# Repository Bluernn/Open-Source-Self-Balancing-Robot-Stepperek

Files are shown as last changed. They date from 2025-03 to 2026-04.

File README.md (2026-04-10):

# Open Source Self-Balancing Robot "Stepperek"

<p align="center">
  Self-balancing robot
</p>

This repository contains an open-source project for a self-balancing robot designed for educational purposes and learning control systems. The project includes both hardware and software components.
## Repository Contents

- **3D Models**  
It contains 3D models of the robot's wheels and motor mounts for 3D printing or further modifications.

- **Schematic and PCB**  
Includes the electrical schematic and all necessary files for manufacturing the PCB.

- **BalancingRobot**  
Contains the complete control program for the self-balancing robot, developed using ESP-IDF v5.2.1. This folder includes the source code and all required files to compile the project.

https://www.youtube.com/watch?v=AlN4MXNQWd8

Shield: [][cc-by-nc]

This work is licensed under a
[Creative Commons Attribution-NonCommercial 4.0 International License][cc-by-nc].

[][cc-by-nc]

[cc-by-nc]: https://creativecommons.org/licenses/by-nc/4.0/
[cc-by-nc-image]: https://licensebuttons.net/l/by-nc/4.0/88x31.png
[cc-by-nc-shield]: https://img.shields.io/badge/License-CC%20BY--NC%204.0-lightgrey.svg

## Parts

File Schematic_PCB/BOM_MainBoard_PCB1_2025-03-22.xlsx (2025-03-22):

No. | Quantity | Comment | Designator | Footprint | Value | Manufacturer Part | Manufacturer | Supplier Part | Supplier
1 | 2 | MY-18650-01 | BT1,BT2 | BAT-TH_MY-18650-01 |  | MY-18650-01 | MYOUNG(美阳) | C2979183 | LCSC
2 | 3 | 10uF | C2,C9,C10 | CASE-A_3216 | 10uF | CA45A-A-16V-10uF-K | CEC(振华新云) | C129279 | LCSC
3 | 7 | 100nF | C8,C20,C21,C35,C37,C39,C40 | C0805 | 100nF | 0805B104K500NT | FH-BK(风华邦科) | C2830721 | LCSC
4 | 1 | 22uF | C12 | CASE-A_3216 | 22uF | CA45-A-10V-22uF-K | CEC(振华新云) | C129272 | LCSC
5 | 6 | 220uF | C19,C26,C32,C34,C38,C41 | CAP-TH_BD6.3-P2.50-D1.0-FD | 220uF | ERS1EM221E11OT | AISHI(艾华集团) | C141282 | LCSC
6 | 2 | 22nF | C22,C28 | C0805 | 22nF | CL21B223KBANNNC | SAMSUNG(三星) | C1729 | LCSC
7 | 8 | 100nF | C23,C24,C25,C27,C29,C30,C31,C33 | C0805 | 100nF | CC0805KRX7R9BB104 | YAGEO(国巨) | C49678 | LCSC
8 | 1 | 680uF | C36 | CAP-TH_BD10.0-P5.00-D1.0-FD | 680uF | ERF1EM681G16OT | AISHI(艾华集团) | C106522 | LCSC
9 | 1 | SS54 | D2 | SMA_L4.4-W2.8-LS5.4-R-RD |  | SS54 | MDD | C22452 | LCSC
10 | 1 | 1N5821RLG | D3 | DO-201AD_BD5.3-L8.4-P12.50-D1.4-RD |  | 1N5821RLG | onsemi(安森美) | C9119 | LCSC
11 | 1 | MSS1P3-M3/89A | D17 | MICROSMP_L2.2-W1.3-LS2.5-RD |  | MSS1P3-M3/89A | VISHAY(威世) | C111315 | LCSC
12 | 1 | 2.54-1*3P针 | H1 | HDR-TH_3P-P2.54-V-M-1 |  | 2.54-1*3P针 | BOOMELE(博穆精密) | C49257 | LCSC
13 | 1 | PM2.54-1*4 | H2 | HDR-TH_4P-P2.54-V-F |  | PM2.54-1*4 | ZHOURI(洲日) | C5116530 | LCSC
14 | 1 | DC3-10P | JTAG | CONN-TH_10P-P1.27_DC3-10P |  | DC3-10P |  | C9900016558 | LCSC
15 | 1 | 2.2uH | L5 | IND-SMD_L2.5-W2.0 | 2.2uH | 252012CDMCDDS-2R2MC | Sumida(胜美达) | C351245 | LCSC
16 | 1 | 100uH | L6 | IND-SMD_L12.3-W12.3_SMDRI127 | 100uH | SMDRI127-101MT | SXN(顺翔诺) | C10150 | LCSC
17 | 2 | 17-21VRD/TR8 | LED1,LED3 | LED0805-R-RD |  | 17-21VRD/TR8 | EVERLIGHT(亿光) | C264415 | LCSC
18 | 2 | SZYY0805YG | LED2,LED6 | LED0805-R-RD_GREEN |  | SZYY0805YG | yongyu(永裕光电) | C434435 | LCSC
19 | 1 | HDR-F-2.54_2x3 | PROGRAMMER | HDR-TH_6P-P2.54-V-F-R2-C3-S2.54
20 | 5 | 1kΩ | R7,R11,R12,R20,R37 | R0805 | 1kΩ | RMC08051K5%N | Tyohm(幸亚电阻) | C269727 | LCSC
21 | 1 | 400mΩ | R10 | R0805 | 400mΩ | CR0805JR400P05Z | EVER OHMS(天二科技) | C175750 | LCSC
22 | 1 | 1.5kΩ | R13 | R0805 | 1.5kΩ | RMC08051.5K5%N | Tyohm(幸亚电阻) | C325846 | LCSC
23 | 2 | 5.1kΩ | R15,R16 | R0805 | 5.1kΩ | CR0805-FX-5101ELF | BOURNS | C204548 | LCSC
24 | 3 | 10kΩ | R21,R29,R36 | R0805 | 10kΩ | ARG05FTC1002 | Viking(光颉) | C217770 | LCSC
25 | 1 | 100Ω | R22 | R0805 | 100Ω | AECR0805F100RK9 | RESI(开步睿思） | C328380 | LCSC
26 | 3 | 2.2kΩ | R27,R30,R31 | R0805 | 2.2kΩ | 0805W8F2201T5E | UNI-ROYAL(厚声) | C17520 | LCSC
27 | 1 | 33kΩ | R28 | R0805 | 33kΩ | 0805W8F3302T5E | UNI-ROYAL(厚声) | C17633 | LCSC
28 | 4 | 1Ω | R32,R33,R34,R35 | R1206 | 1Ω | 1206W4F100KT5E | UNI-ROYAL(厚声) | C17928 | LCSC
29 | 1 | SK12D07VG4 | SW1 | SW-TH_SK12D07VG4 |  | SK12D07VG4 | SHOU HAN(首韩) | C393937 | LCSC
30 | 1 | ESP32-WROOM-32E-N4 | U1 | WIFI-SMD_ESP32-WROOM-32E |  | ESP32-WROOM-32E-N4 | ESPRESSIF(乐鑫) | C701341 | LCSC
31 | 2 | B04B-XASK-1(LF)(SN) | U5,U6 | CONN-TH_B04B-XASK-1-LF-SN |  | B04B-XASK-1(LF)(SN) | JST | C264994 | LCSC
32 | 1 | CFS12V3T5R0 | U14 | F1206 |  | CFS12V3T5R0 | 大毅科技 | C163128 | LCSC
33 | 1 | TP4056 | U19 | ESOP-8_L4.9-W3.9-P1.27-LS6.0-BL-EP |  | TP4056 | UMW(友台半导体) | C725790 | LCSC
34 | 1 | TYPEC-250Y-BRP6L68 | U20 | TYPE-C-SMD_XUNPU_TYPEC-250Y-BRP6L68 |  | TYPEC-250Y-BRP6L68 | XUNPU(讯普) | C5252714 | LCSC
35 | 1 | 0466005.NR | U21 | F1206 |  | 0466005.NR | Littelfuse(美国力特) | C187597 | LCSC
36 | 1 | TPS63001DRCR | U27 | VSON-10_L3.0-W3.0-P0.50-TL-EP_TPS62410DRCR |  | TPS63001DRCR | TI(德州仪器) | C28060 | LCSC
37 | 2 | TMC2226-SA-T | U28,U30 | HTSSOP-28_L9.8-W4.5-P0.65-LS6.6-BL-EP |  | TMC2226-SA-T | TRINAMIC | C705366 | LCSC
38 | 2 | 2.2uF | U29,U31 | CAP-SMD_L3.2-W1.6-RD-1 | 2.2uF | CA45A-A-16V-2.2UF-K | CEC(振华新云) | C2976909 | LCSC
39 | 1 | LM2577S-ADJ | U32 | TO-263-5_L10.6-W8.4-P1.70-LS13.7 |  | LM2577S-ADJ | Slkor(萨科微) | C5122561 | LCSC
40 | 1 | BMI160 | U33 | LGA-14_L3.0-W2.5-P0.50-BL |  | BMI160 | Bosch(博世) | C94021 | LCSC

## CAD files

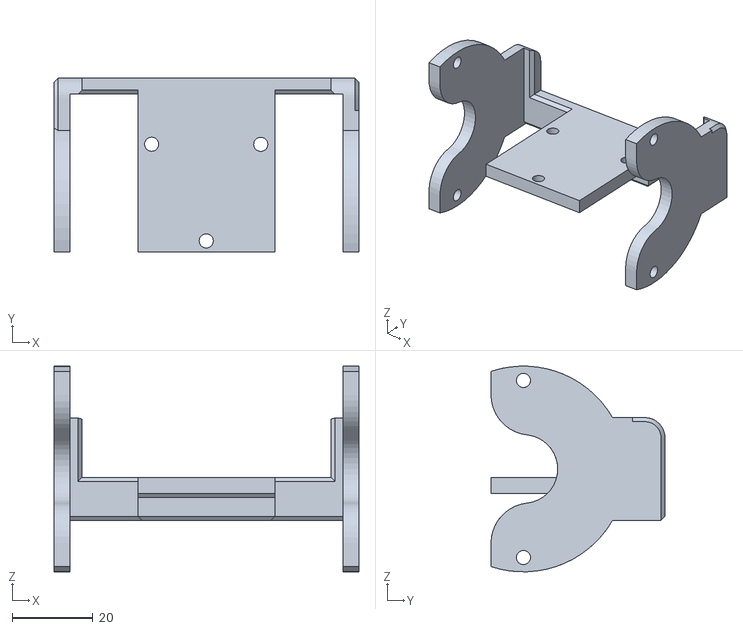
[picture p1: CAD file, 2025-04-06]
3D_Print/motor_mount.STL
75.6 x 43.1 x 51.0

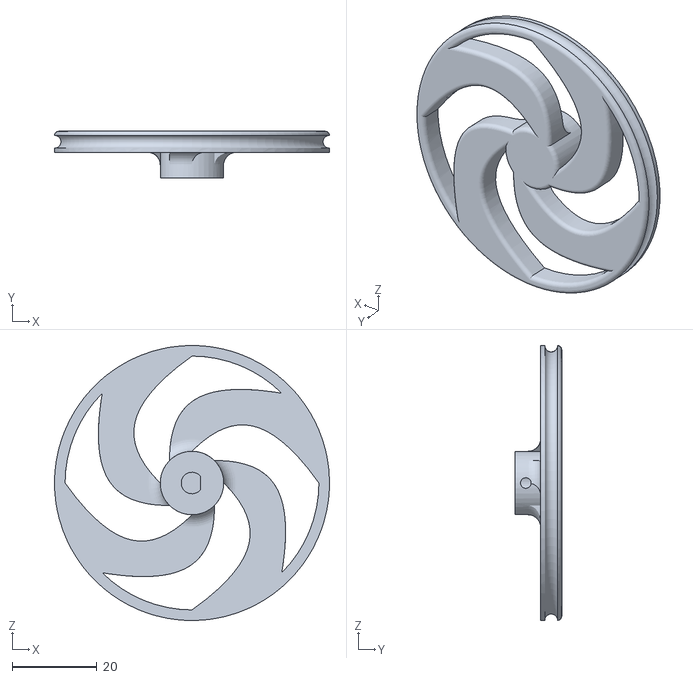
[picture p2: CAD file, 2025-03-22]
3D_Print/wheel.STL
65.0 x 11.0 x 65.0

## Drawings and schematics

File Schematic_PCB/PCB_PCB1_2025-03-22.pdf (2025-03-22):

+

# Power

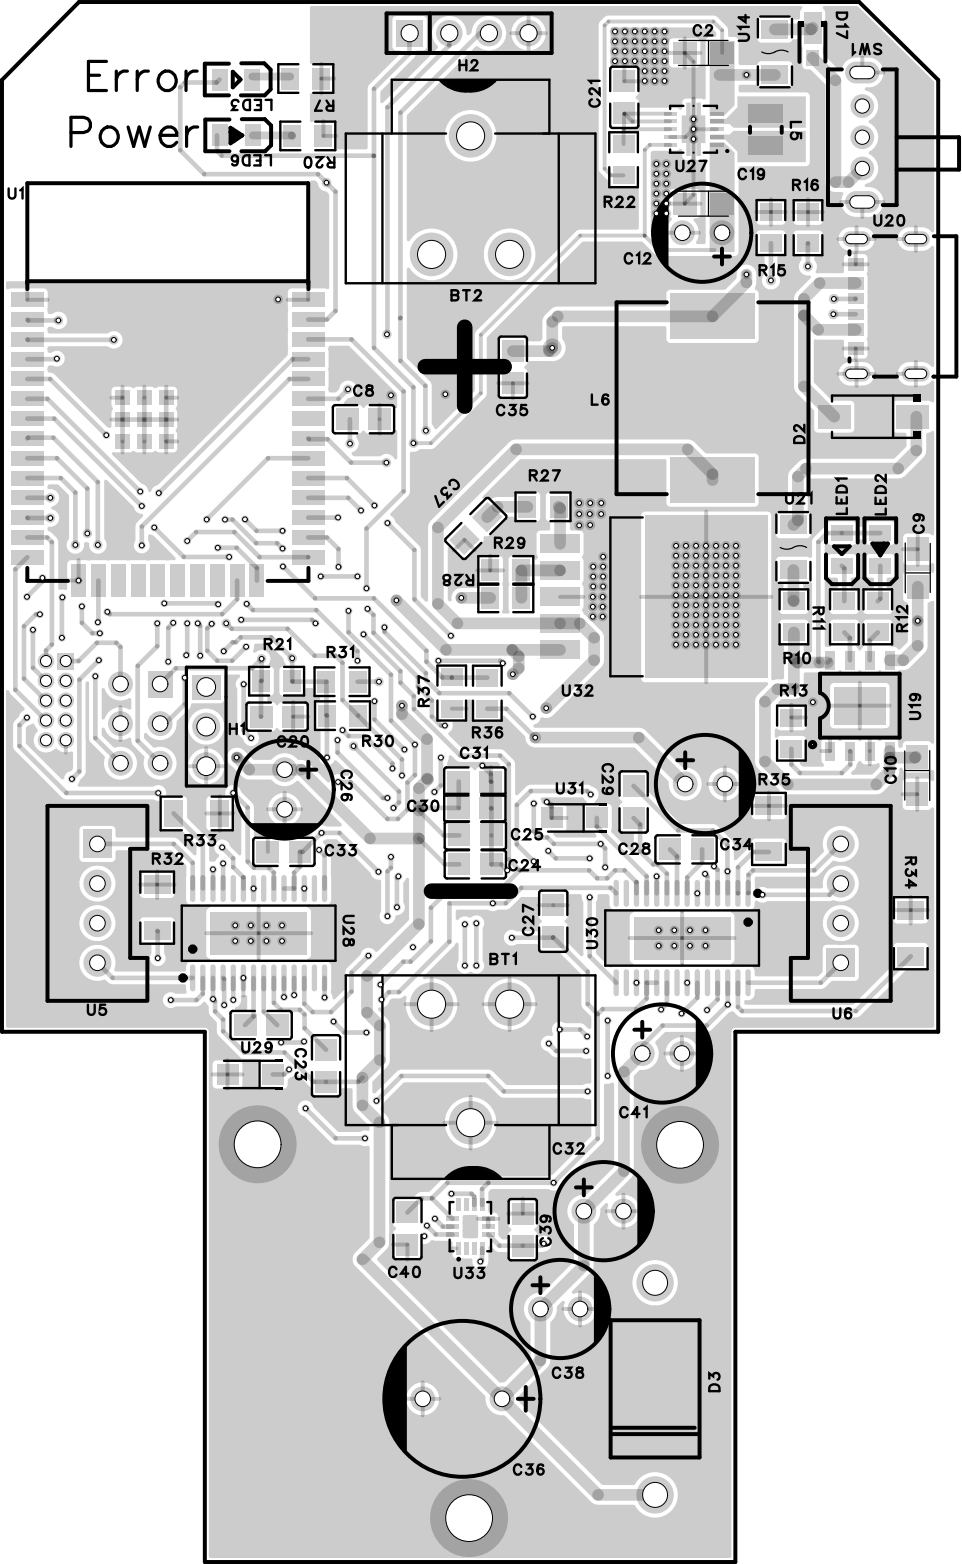
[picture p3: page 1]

# SelfBalancingRobot v0.9

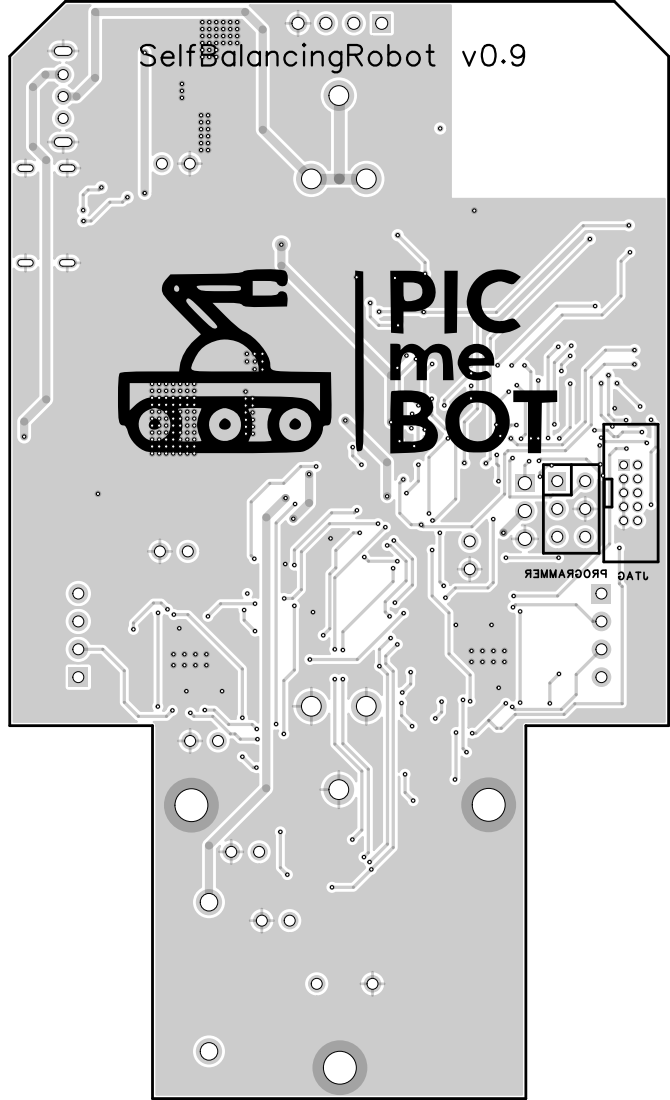
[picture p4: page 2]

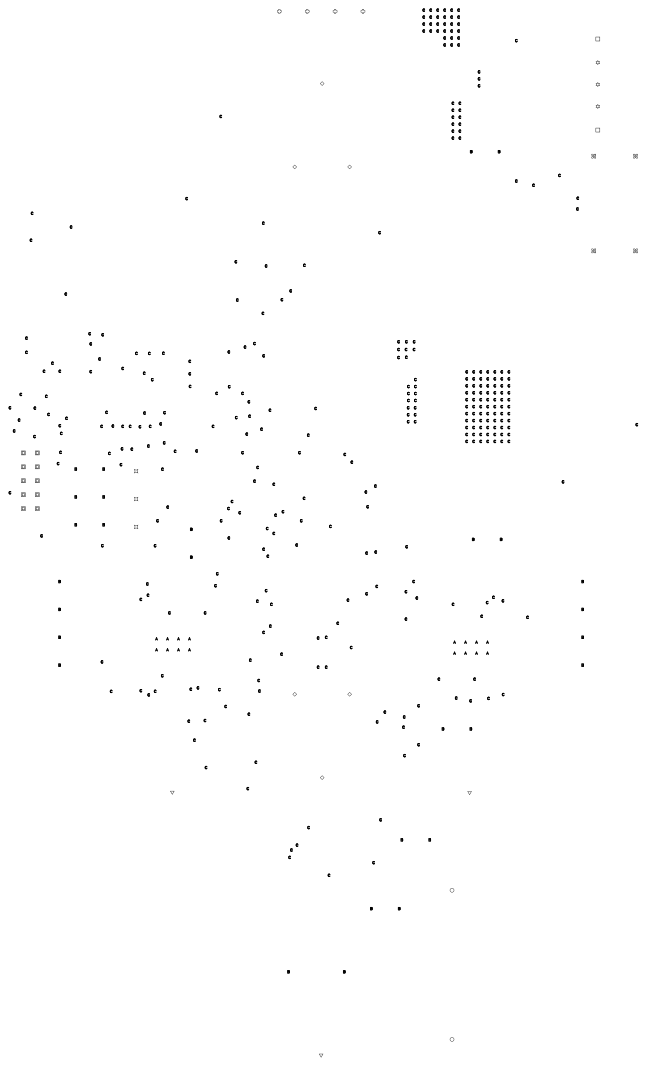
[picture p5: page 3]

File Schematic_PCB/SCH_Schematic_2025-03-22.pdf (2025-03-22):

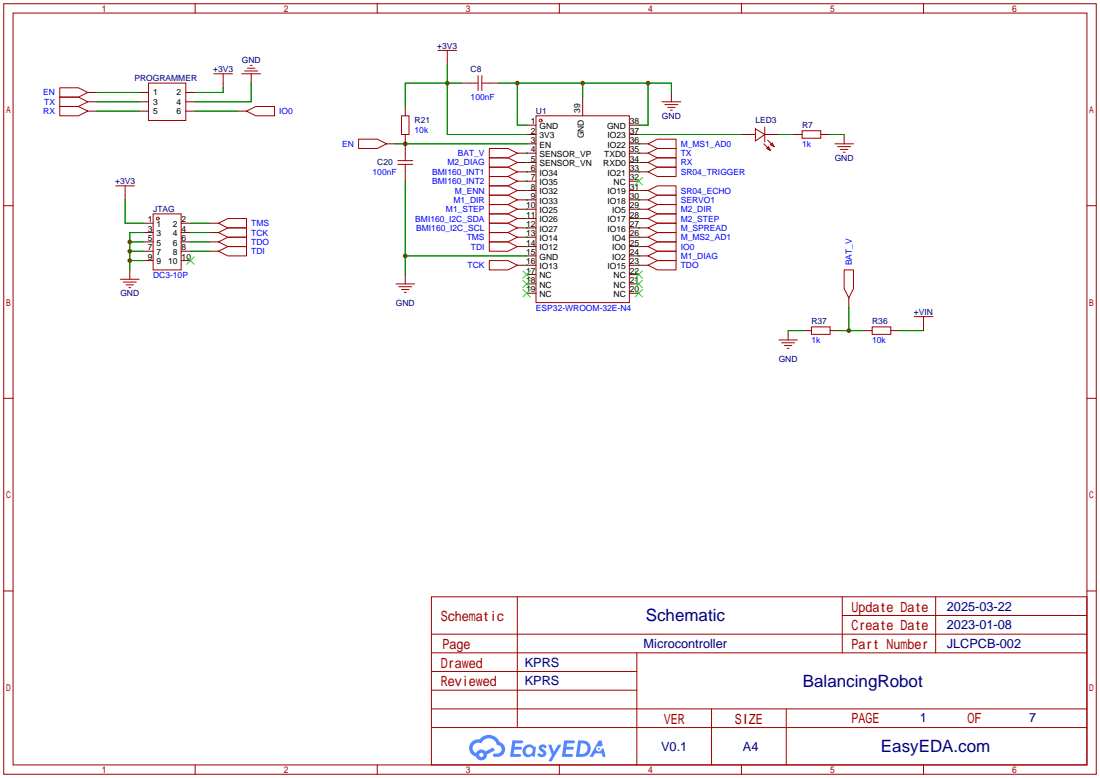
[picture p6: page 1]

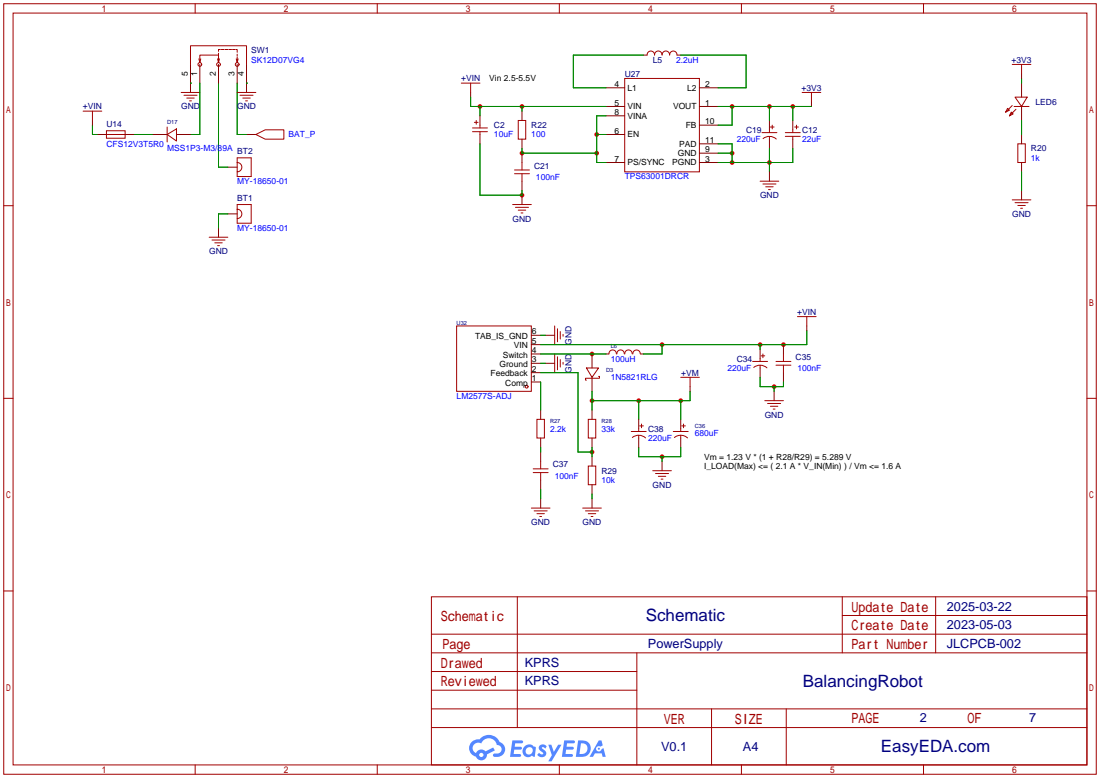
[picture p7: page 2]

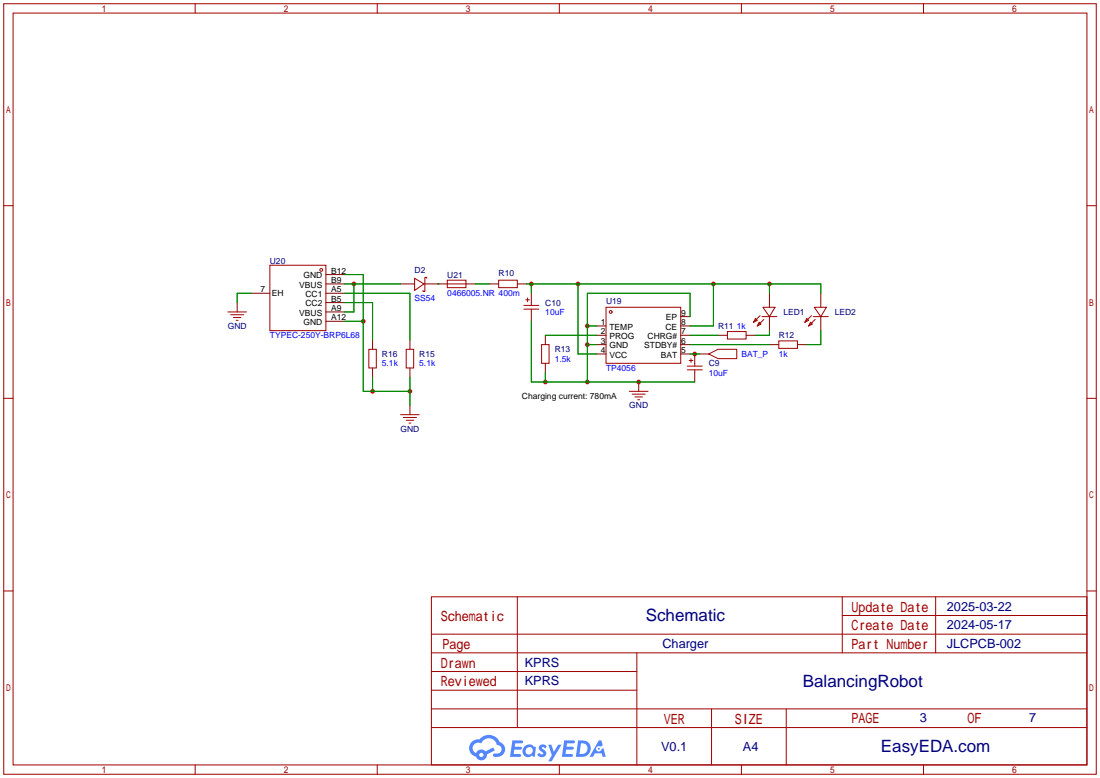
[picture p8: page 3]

# GND GND

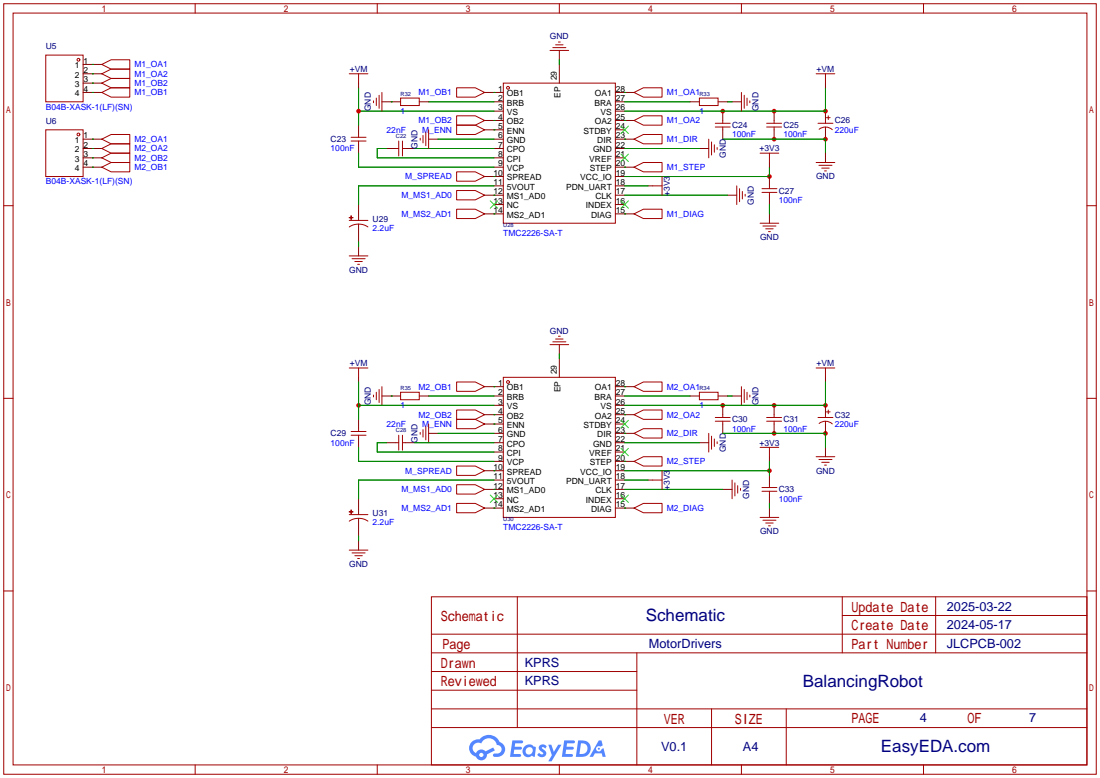
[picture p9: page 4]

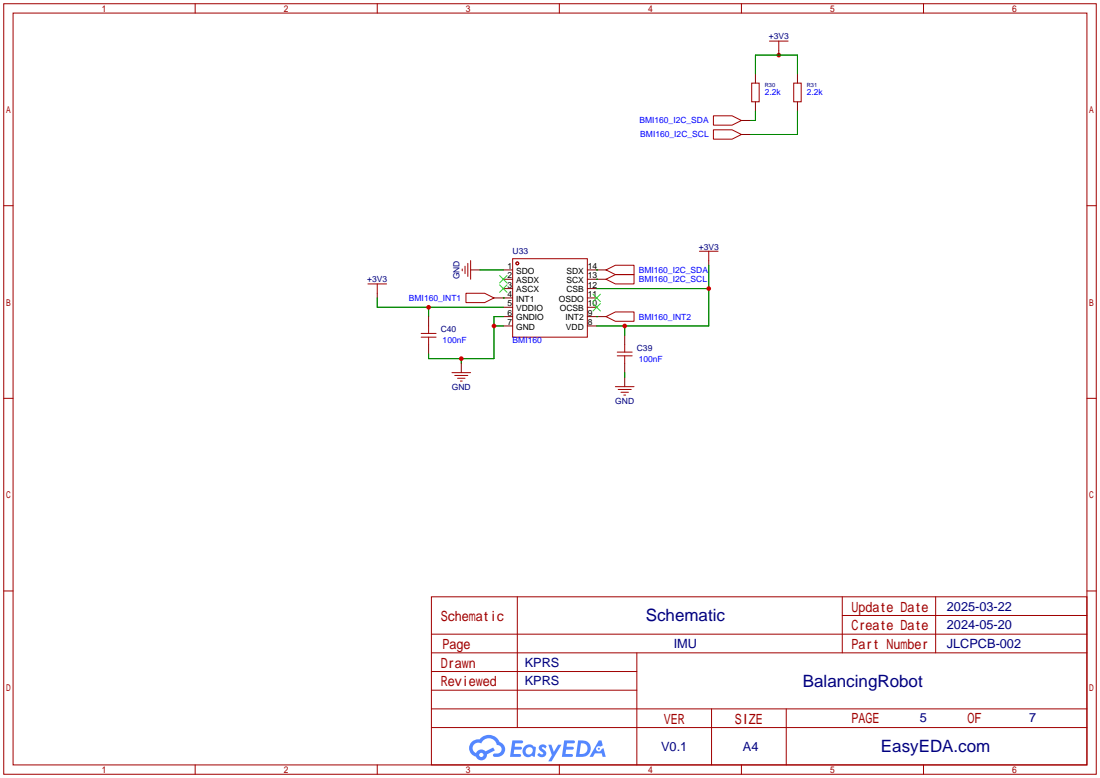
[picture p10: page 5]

OCSB 10 OSDO 11 CSB 12 SCX 13 SDX 14

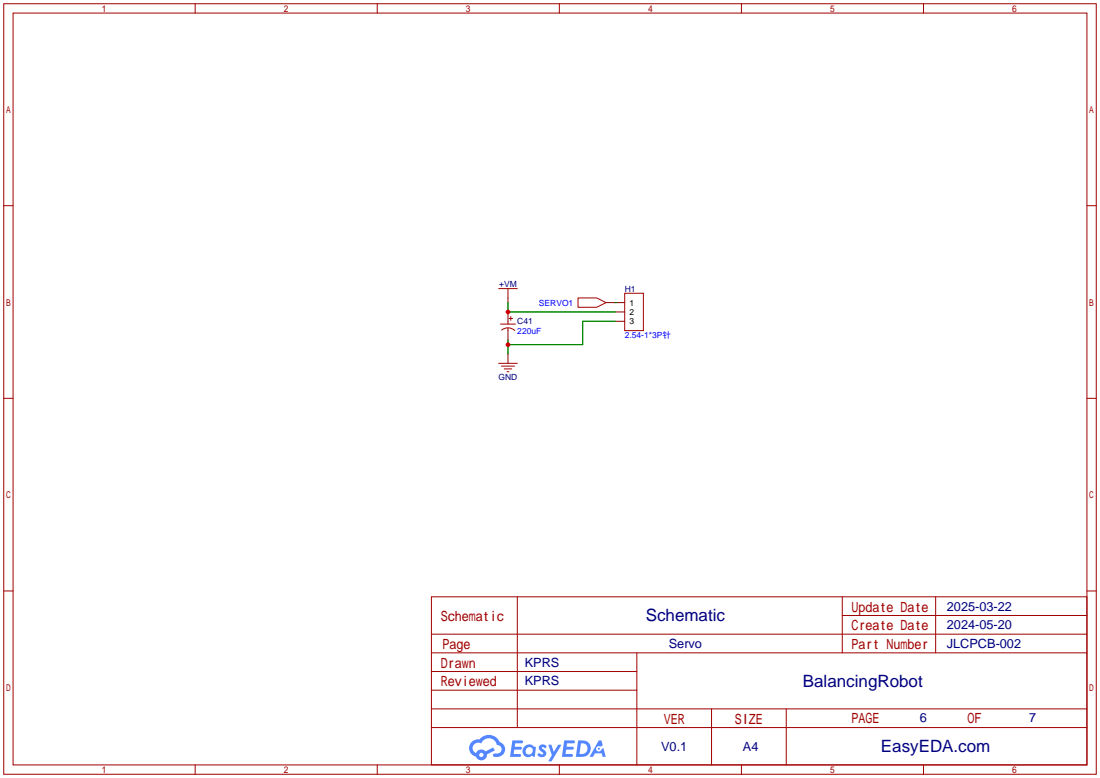
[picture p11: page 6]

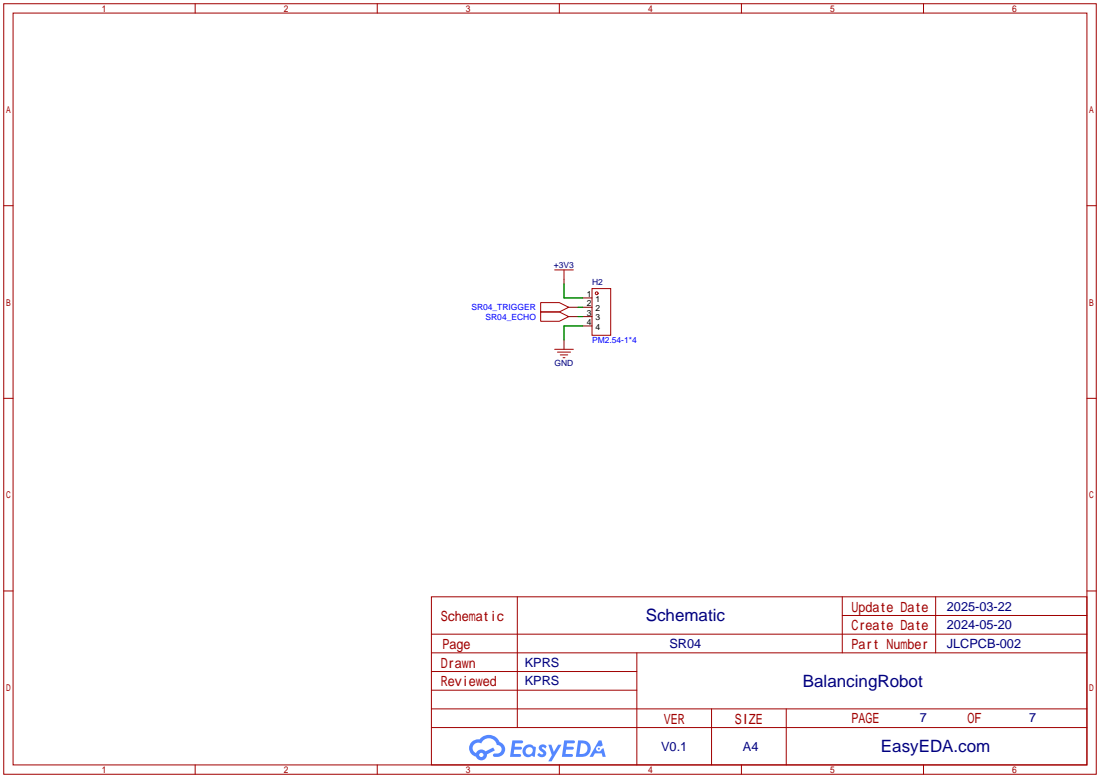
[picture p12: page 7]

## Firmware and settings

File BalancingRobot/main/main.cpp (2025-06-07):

#include <inttypes.h>
#include <cstring>
#include "freertos/FreeRTOS.h"
#include "freertos/task.h"
#include "freertos/queue.h"
#include "freertos/message_buffer.h"
#include "esp_log.h"
#include <esp_timer.h>
#include "driver/i2c.h"
#include "cJSON.h"

#include "websocket_server.h"
#include "mdns.h"
#include "../components/pinManager/pinManager.h"
#include "../components/stepperMotorController/stepperMotorController.h"
#include "../components/webServerClient/webServerClient.h"
#include "../components/controllers/controllers.h"
#include "../components/adcReader/adcReader.h"

static const char *TAG = "MAIN";
static const char *MDNS_HOSTNAME = "selfbalancingrobot";

MessageBufferHandle_t xMessageBufferToClient;

extern "C" {
	void app_main(void);
}

void bmi160(void *pvParameters);
void BMI_send_data(void *pvParameters);

#ifdef __cplusplus
extern "C" {
#endif
void start_mdns(void);
void start_i2c(void);
int ws_server_start(void);
#include "../components/wifi/wifi.h"
#include "../components/ultrasonic/ultrasonic.h"
#ifdef __cplusplus
}
#endif

void start_mdns(void)
{
	//initialize mDNS
	ESP_ERROR_CHECK( mdns_init() );
	//set mDNS hostname (required if you want to advertise services)
	ESP_ERROR_CHECK( mdns_hostname_set(MDNS_HOSTNAME) );
	ESP_LOGI(TAG, "mdns hostname set to: [%s]", MDNS_HOSTNAME);

	//initialize service
	ESP_ERROR_CHECK( mdns_service_add(NULL, "_http", "_tcp", 80, NULL, 0) );
}

void start_i2c(void) {
	i2c_config_t conf;
	conf.mode = I2C_MODE_MASTER;
	conf.sda_io_num = (gpio_num_t)BMI160_I2C_SDA;
	conf.scl_io_num = (gpio_num_t)BMI160_I2C_SCL;
	conf.sda_pullup_en = GPIO_PULLUP_ENABLE;
	conf.scl_pullup_en = GPIO_PULLUP_ENABLE;
	conf.master.clk_speed = 400000;
	conf.clk_flags = 0;
	ESP_ERROR_CHECK(i2c_param_config(I2C_NUM_0, &conf));
	ESP_ERROR_CHECK(i2c_driver_install(I2C_NUM_0, I2C_MODE_MASTER, 0, 0, 0));
}

extern volatile RobotMode currentMode;
extern volatile bool isStable;
extern volatile int robotEnable;
extern volatile PStructure Position;
extern volatile PIStructure Velocity;
extern volatile PDStructure Angle;
extern volatile double setPosition;
extern volatile double setTestValue;
extern volatile double setVelocity;
extern volatile double setVelocityTurnFactor;
extern volatile bool isStation;
extern volatile double roll;
//extern volatile float rawRoll;

// Define queue to share data between tasks
QueueHandle_t dataQueue;

// Data structure for storing IMU values
typedef struct {
    double p_ref, p, v_ref, v, O_ref, O, a;
} SensorData;

void IRAM_ATTR timerCallbackSD(void *arg) {
	if (!isStation) return;
	
    // Data preparation
	SensorData data = {
		.p_ref = Position.SetpointValue,
		.p = Position.MeasuredValue,
		.v_ref = Velocity.SetpointValue,
		.v = Velocity.MeasuredValue,
		//.O_ref = rawRoll,
		.O_ref = Angle.SetpointValue,
		.O = roll,
		.a = Angle.OutputValue
	};
	
    // Sending data to the queue
    BaseType_t xHigherPriorityTaskWoken = pdFALSE;
    if (xQueueSendFromISR(dataQueue, &data, &xHigherPriorityTaskWoken) != pdPASS) {
		ESP_LOGE(TAG, "Queue send failed in ISR");
    }

    // Force context switching, if necessary
    if (xHigherPriorityTaskWoken) {
        portYIELD_FROM_ISR();
    }
}

void setupTimerSD() {
	ESP_LOGI(TAG, "Starting setupTimerSD ...");
    const esp_timer_create_args_t timer_argsSD = {
        .callback = &timerCallbackSD,
        .arg = NULL,               
        .dispatch_method = ESP_TIMER_TASK,
        .name = "sensor_timer"
    };

    esp_timer_handle_t timer_handleSD;
    ESP_ERROR_CHECK(esp_timer_create(&timer_argsSD, &timer_handleSD));
    ESP_ERROR_CHECK(esp_timer_start_periodic(timer_handleSD, 10000));

	ESP_LOGI(TAG, "setupTimerSD timer initialized.");
}

void sequenceTimerCallback(void *arg) {
    static int state = 0;

    // Check if the control is active
    if (!isStable && robotEnable == 0) {
        Velocity.SetpointValue = 0.0;
		state = 0;
        return;
    }

	if ( currentMode == QUADRANT_SEQUENCE_MODE ) // - change timer to 1 s
	{
		switch (state) {
			case 0: 
				setVelocityTurnFactor = 0;
				state = 1;
				break; 
			case 1:
				setVelocityTurnFactor = 0.5;
				state = 0;
			break; 
		}
	}
    else if (currentMode == TEST_MODE_VELOCITY) {  // FOR TESTING VELOCITY CONTROLLER - change timer to 5 s
        switch (state) {
            case 0:
                Velocity.SetpointValue = 0.0; // Stop
                state = 1;
                break;
            case 1:
                Velocity.SetpointValue = setTestValue; // Move backward
                state = 2;
                break;
			case 2:
			    state = 3;
                break;
            case 3:
                Velocity.SetpointValue = 0.0; // Stop
                state = 4;
                break;
            case 4:
                Velocity.SetpointValue = -setTestValue; // Move forward
                state = 5;
                break;
			case 5:
			    state = 0;
                break;
        }
    }
    else if (currentMode == TEST_MODE_POSITION) {  // FOR TESTING POSITION CONTROLLER - change timer to 10 s
        switch (state) {
            case 0:
				Position.SetpointValue = 0.0; // Stop
                state = 1;
                break;
            case 1:
				Position.SetpointValue = setTestValue; // Move backward
                state = 2;
                break;
            case 2:
				Position.SetpointValue = 0.0; // Stop
                state = 3;
                break;
            case 3:
				Position.SetpointValue = -setTestValue; // Move forward
                state = 0;
                break;
        }
    }
}

void setupSequenceTimer() {
	ESP_LOGI(TAG, "Starting setupSequenceTimer...");
    
    const esp_timer_create_args_t sequence_timer_args = {
        .callback = &sequenceTimerCallback,
        .arg = NULL,
        .dispatch_method = ESP_TIMER_TASK,
        .name = "sequence_timer"
    };

	esp_timer_handle_t sequence_timer_handle;
    ESP_ERROR_CHECK(esp_timer_create(&sequence_timer_args, &sequence_timer_handle));
    
    ESP_ERROR_CHECK(esp_timer_start_periodic(sequence_timer_handle, 1000000)); // sec

	ESP_LOGI(TAG, "setupSequenceTimer initialized.");
}

#define MAX_DISTANCE_M 5 // 5m max
volatile float ultrasonicDistance = 0.0f;
ultrasonic_sensor_t ultrasonicSensor = {
	.trigger_pin = SR04_TRIGGER,
	.echo_pin = SR04_ECHO
};

void UltrasonicTask(void *pvParameters)
{
    while(1) {
		float distance;
		esp_err_t res = ultrasonic_measure_m(&ultrasonicSensor, MAX_DISTANCE_M, &distance);

		if ( res == ESP_OK )
			ultrasonicDistance = distance;

		if (currentMode == SENSOR_MODE)
			vTaskDelay(pdMS_TO_TICKS(100));
		else
			vTaskDelay(pdMS_TO_TICKS(1000));
    }
}

// Task responsible for sending data every 2 ms
void SendDataTask(void *pvParameters) {
    SensorData data;

    while (1) {
        if (dataQueue != NULL)
        {
            // Try receiving data from the queue
            if (xQueueReceive(dataQueue, &data, portMAX_DELAY) == pdPASS) {
                // Prepare JSON data
                cJSON *request = cJSON_CreateObject();
                cJSON_AddStringToObject(request, "id", "data-request");
                cJSON_AddNumberToObject(request, "p_ref", data.p_ref);
                cJSON_AddNumberToObject(request, "p", data.p);
                cJSON_AddNumberToObject(request, "v_ref", data.v_ref);
                cJSON_AddNumberToObject(request, "v", data.v);
                cJSON_AddNumberToObject(request, "O_ref", data.O_ref);
                cJSON_AddNumberToObject(request, "O", data.O);
                cJSON_AddNumberToObject(request, "a", data.a*0.001);

                // Convert JSON to string
                char *my_json_string = cJSON_Print(request);

                // Send data over the message buffer
                size_t xBytesSent = xMessageBufferSend(xMessageBufferToClient, my_json_string, strlen(my_json_string), 100);
                if (xBytesSent != strlen(my_json_string)) {
                    ESP_LOGE(TAG, "Failed to send message buffer");
                }

                // Free resources
                cJSON_Delete(request);
                cJSON_free(my_json_string);
            }        
        }

        vTaskDelay(pdMS_TO_TICKS(2));
    }

    vTaskDelete(NULL);
}

void app_main(void)
{
	// Create a queue to hold 10 SensorData element
	dataQueue = xQueueCreate(64, sizeof(SensorData));

	// Initialize ESP Pins
	PM_Configuration();

	// Initialize ADC
	ADC_ReaderInit();

	// Initialize StepperMotors
	SMC_StepperInit();

	// Initialize WiFi
	setup_wifi();

	// Initialize mDNS
	start_mdns();

	// Initialize i2c
	start_i2c();

	// Initialize ultrasonic
	ultrasonic_init(&ultrasonicSensor);

	// Create Message Buffer
	xMessageBufferToClient = xMessageBufferCreate(1024*4);
	configASSERT( xMessageBufferToClient );

	// Start web socket server
	ws_server_start();

	// Start web server
	xTaskCreate(&server_task, "SERVER", 1024*2, NULL, 5, NULL);

	// Start web client
	xTaskCreate(&client_task, "CLIENT", 1024*3, (void *)0x011, 5, NULL);

	// Start imu task
	xTaskCreate(&bmi160, "IMU", 1024*8, NULL, 5, NULL);

	xTaskCreate(StabilityMonitorTask, "StabilityMonitor", 2048, NULL, 5, NULL);

	xTaskCreate(&SMC_StepperControl, "StepperControl", 1024*8, NULL, 5, NULL);

	xTaskCreate(SendDataTask, "Send Data Task", 1024*4, NULL, 5, NULL);

	xTaskCreate(UltrasonicTask, "Ultrasonic Task", 1024*2, NULL, 5, NULL);

	xTaskCreate(ADC_TaskStart, "adc_task", 2048, NULL, 4, NULL);

	setupTimerSD();
	setupSequenceTimer();
}

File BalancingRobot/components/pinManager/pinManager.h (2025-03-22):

#ifndef PINMANAGER_H
#define	PINMANAGER_H

#define M1_DIAG GPIO_NUM_36
#define M2_DIAG GPIO_NUM_39
#define BMI160_INT1 GPIO_NUM_34
#define BMI160_INT2 GPIO_NUM_35
#define M_EN GPIO_NUM_32
#define M1_DIR GPIO_NUM_33
#define M1_STEP GPIO_NUM_25
#define BMI160_I2C_SDA GPIO_NUM_26
#define BMI160_I2C_SCL GPIO_NUM_27
#define M_MS2_AD1 GPIO_NUM_4
#define M_SPREAD GPIO_NUM_16
#define M2_STEP GPIO_NUM_17
#define M2_DIR GPIO_NUM_5
#define SERVO1 GPIO_NUM_18
#define SR04_ECHO GPIO_NUM_19
#define SR04_TRIGGER GPIO_NUM_21
#define M_MS1_AD0 GPIO_NUM_22
#define ERROR_PIN GPIO_NUM_23

void PM_Configuration(void);

#endif

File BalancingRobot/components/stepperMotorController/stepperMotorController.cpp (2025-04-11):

#include "stepperMotorController.h"

#include "freertos/FreeRTOS.h"
#include "freertos/task.h"
#include "driver/gpio.h"
#include "../pinManager/pinManager.h"
#include "driver/ledc.h"
#include "esp_log.h"
#include <esp_timer.h>

#include "../controllers/controllers.h"

#define MOTORS_ENABLE   gpio_set_level(M_EN, 0);
#define MOTORS_DISABLE  gpio_set_level(M_EN, 1);

#define DIR_1_FORWARD   gpio_set_level(M1_DIR, 0);
#define DIR_1_BACKWARD  gpio_set_level(M1_DIR, 1);
#define DIR_2_FORWARD   gpio_set_level(M2_DIR, 1);
#define DIR_2_BACKWARD  gpio_set_level(M2_DIR, 0)

//200 steps/rev motor with microstepping 1/8 = 1600
#define STEPS_NUMBER_PER_ROTATION (32*200)
#define WHEEL_RADIUS 0.0335 // m
#define TWO_PI 6.283185307179586476925286766559

#define STABILITY_CHECK_TIME_MS 3000 // 3 seconds to check if the robot has returned to a stable position
#define STABILITY_TOLERANCE 5 // Tolerance range in degrees for stability

#define MAX_PWM_FREQ 70000

extern volatile bool lowVoltage;
extern volatile double setVelocity;
extern volatile double setVelocityTurnFactor;
extern volatile double setPosition;
extern volatile float ultrasonicDistance;
volatile int robotEnable = 0; // WEB ON 
volatile bool robotStable = false;
volatile double angularVelocity = 0, acceleration = 0;
volatile bool controlEnable = false;
volatile bool isStable = false; // Flag to enable motor control after stability check
volatile TickType_t stabilityCheckStartTime = 0;

volatile uint16_t m1Freq = 1000;
volatile uint16_t m2Freq = 1000;
volatile uint8_t PWMDutyMotor1 = 0;
volatile uint8_t PWMDutyMotor2 = 0;

extern volatile double roll;
extern volatile RobotMode currentMode;

extern volatile PDStructure Angle;
extern volatile PIStructure Velocity;
extern volatile PStructure Position;

static const char *SMC_TAG = "stepperMotorController";

/* 0 - 1/8, 
1 - 1/16, 
2 - 1/32, 
3 - 1/64 */
static void SMC_MicrostepResolutionConfiguration(uint8_t config)
{
    ESP_LOGI(SMC_TAG,"SMC_MicrostepResolutionConfiguration... ");

    switch (config)
    {
    case 1: // 1/16
        gpio_set_level(M_MS1_AD0, 1);
        gpio_set_level(M_MS2_AD1, 1);
        break;
    case 2: // 1/32
        gpio_set_level(M_MS1_AD0, 1);
        gpio_set_level(M_MS2_AD1, 0);
        break;
    case 3: // 1/64
        gpio_set_level(M_MS1_AD0, 0);
        gpio_set_level(M_MS2_AD1, 1);
        break;
    default: // 1/8
        gpio_set_level(M_MS1_AD0, 0);
        gpio_set_level(M_MS2_AD1, 0);
        break;
    }

    ESP_LOGI(SMC_TAG, "SMC_MicrostepResolutionConfiguration COMPLETE!");
}

static void SMC_PWMConfig(void)
{
    ESP_LOGI(SMC_TAG,"SMC_PWMConfig... ");

    // PWM channel configuration for the first STEP
    ledc_timer_config_t ledc_timer1 = {
        .speed_mode = LEDC_HIGH_SPEED_MODE,
        .duty_resolution = LEDC_TIMER_10_BIT,
        .timer_num = LEDC_TIMER_0,
        .freq_hz = m1Freq,
        .clk_cfg = LEDC_AUTO_CLK
    };

    ESP_ERROR_CHECK(ledc_timer_config(&ledc_timer1));

    ledc_channel_config_t ledc_channel1 = {
        .gpio_num = M1_STEP,
        .speed_mode = LEDC_HIGH_SPEED_MODE,
        .channel = LEDC_CHANNEL_0,
        .timer_sel = LEDC_TIMER_0,
        .duty = PWMDutyMotor1,
        .hpoint = 0
    };
    ESP_ERROR_CHECK(ledc_channel_config(&ledc_channel1));

    // PWM channel configuration for the second STEP
    ledc_timer_config_t ledc_timer2 = {
        .speed_mode = LEDC_HIGH_SPEED_MODE,
        .duty_resolution = LEDC_TIMER_10_BIT,
        .timer_num = LEDC_TIMER_1,
        .freq_hz = m2Freq,
        .clk_cfg = LEDC_AUTO_CLK
    };
    ESP_ERROR_CHECK(ledc_timer_config(&ledc_timer2));

    ledc_channel_config_t ledc_channel2 = {
        .gpio_num = M2_STEP,
        .speed_mode = LEDC_HIGH_SPEED_MODE,
        .channel = LEDC_CHANNEL_1,
        .timer_sel = LEDC_TIMER_1,
        .duty = PWMDutyMotor2,
        .hpoint = 0
    };
    ESP_ERROR_CHECK(ledc_channel_config(&ledc_channel2));

    ESP_LOGI(SMC_TAG, "SMC_PWMConfig COMPLETE!");
}

void SMC_StepperInit(void)
{   
    ESP_LOGI(SMC_TAG,"SMC_StepperInit... ");

    SMC_MicrostepResolutionConfiguration(2);
    SMC_PWMConfig();

    MOTORS_DISABLE;

    DIR_1_FORWARD;
    DIR_2_FORWARD;

    C_init();

    ESP_LOGI(SMC_TAG, "SMC_StepperInit COMPLETE!");
}

static void SMC_SetMotorsPWMDuty(uint8_t motor, uint16_t tmpDuty)
{
    // Select channel based on motor number
    ledc_channel_t channel = (motor == 1) ? LEDC_CHANNEL_0 : LEDC_CHANNEL_1;

    // Get the current PWM for the selected channel
    uint32_t currentDuty = ledc_get_duty(LEDC_HIGH_SPEED_MODE, channel);

    // Update only if PWM is different from tmpDuty
    if (currentDuty != tmpDuty)
    {
        ledc_set_duty(LEDC_HIGH_SPEED_MODE, channel, tmpDuty);
        ledc_update_duty(LEDC_HIGH_SPEED_MODE, channel);

        // Update the value of the stored PWM for a given motor
        if (motor == 1) PWMDutyMotor1 = tmpDuty;
        else PWMDutyMotor2 = tmpDuty;
    }
}

void StabilityMonitorTask(void *param) {
    while (true) {
        if (controlEnable == false)
        {
            if (roll >= STABILITY_TOLERANCE || roll <= -STABILITY_TOLERANCE) {
                // Robot is not stable, reset the time
                stabilityCheckStartTime = xTaskGetTickCount();
                isStable = false;
            } else {
                // Check if the robot was stable for a set period of time
                if ((xTaskGetTickCount() - stabilityCheckStartTime) >= pdMS_TO_TICKS(STABILITY_CHECK_TIME_MS)) {
                    isStable = true;
                }
            }
        }
        vTaskDelay(pdMS_TO_TICKS(1000));
    }
}
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

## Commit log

2025-03-22 All project
    [BOM_MainBoard_PCB1_2025-03-22.xlsx, PickAndPlace_PCB1_2025-03-22.xlsx, motor_mount .STL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]
2025-04-05 - Addition of battery voltage value reading - component adcReader - Modify Gyro and Accel Output Data Rate - IMU OFFSET - Modify micro-stepping to 1/64
2025-04-06 Motor mount Update
    [motor_mount .STL, motor_mount.STL]

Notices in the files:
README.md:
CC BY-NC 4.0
